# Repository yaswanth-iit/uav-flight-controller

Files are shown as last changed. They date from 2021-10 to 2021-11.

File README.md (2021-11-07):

## UAV Flight Controller
This repository consists of schematics, PCB layout, output files of UAV flight controller (Designed using kiCAD) [4-Layer]

[Schematics](https://raw.githubusercontent.com/yaswanth-iit/uav-flight-controller/master/quick%20view/schematics.pdf)

[PCB Layout](https://raw.githubusercontent.com/yaswanth-iit/uav-flight-controller/master/quick%20view/full%20pcb%20layout.pdf)

Used ICs:

* Microcontroller:  STM32F405RGT6, 25 MHz Clock
* EEPROM: 24CW1280T-I_OT
* FLASH Memory: W25N01GVZEIG_TR
* IMU: BMI088
* Magnetometer: IIS2MDCTR
* Barometer: BMP388
* PWM DRIVER: PCA9685BS
* SBUS INVERTER: 74LVC1G04GX4Z
* Voltage Regulator: LD39200PU33R
* USB TO UART: CH330
* ESD Suppressor: USBLC6-2SC6

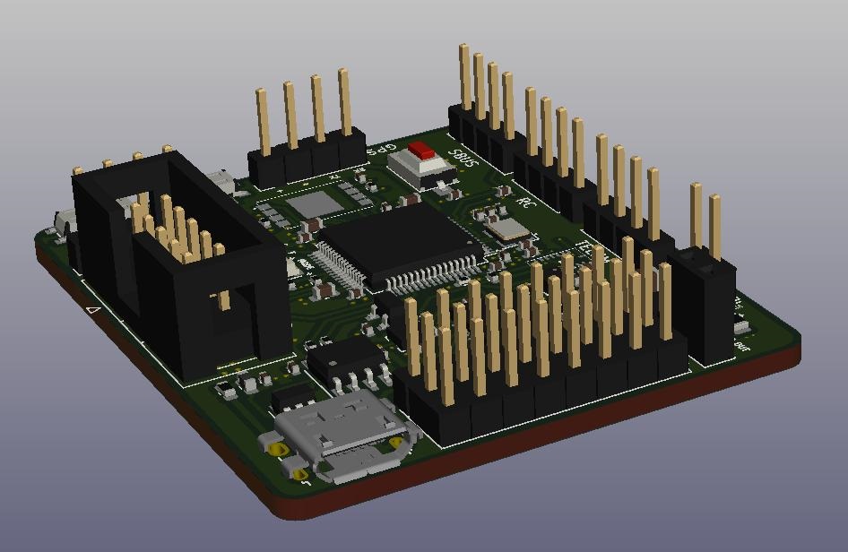
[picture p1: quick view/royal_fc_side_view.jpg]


# Top View

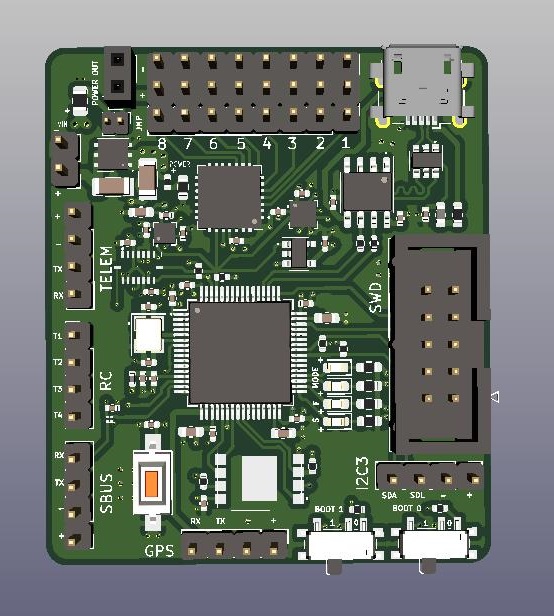
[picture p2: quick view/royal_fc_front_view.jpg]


# Bottom view

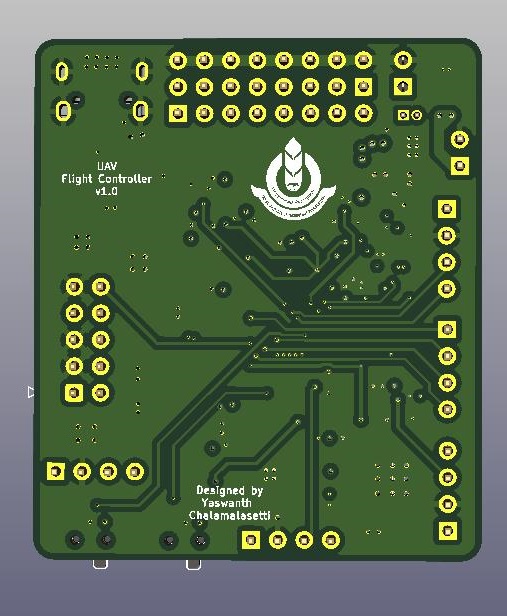
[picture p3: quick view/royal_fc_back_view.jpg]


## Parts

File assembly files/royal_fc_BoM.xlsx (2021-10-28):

Item | Qty | Reference(s) | Value | Description | Component name : PCB footprint | Manufacturer | Part Number | Availability status | Distributor
1 | 20 | C1, C3, C4, C5, C6, C8, C9, C14, C15, C16, C17, C18, C21, C22, C23, C24, C25, C26, C28, C29, | 100nF | 4.7uF+/-10% 10V X5R 1608 0603 | Capacitor_SMD:C_0402_1005Metric
2 | 1 | C2, | 4.7uF | 1UF 16V 10% 0402 | Capacitor_SMD:C_0603_1608Metric
3 | 1 | C7, | 1uF | 16V 0.1uF X5R 0402 10% | Capacitor_SMD:C_0402_1005Metric
4 | 2 | C10, C11, | 10uF | 2.2uF+/-10% 16V X5R 1608 0603 | Capacitor_SMD:C_1206_3216Metric
5 | 2 | C12, C13, | 2.2uF | 50V 18pF C0G 0402 5% | Capacitor_SMD:C_0603_1608Metric
6 | 2 | C19, C20, | 18pF | 1206 MLCC X5R 10 uF +/- 5% 10 V | Capacitor_SMD:C_0402_1005Metric
7 | 1 | C27, | 10uF | 0603 10uF+/-10% 10V X5R 1608 | Capacitor_SMD:C_0603_1608Metric
8 | 1 | C30, | 220nF | 10V 0.22uF X5R 0402 10% | Capacitor_SMD:C_0402_1005Metric
9 | 1 | D1, | Yellow | Light emitting diode | Fuse:Fuse_0402_1005Metric
10 | 1 | D2, | Green | Light emitting diode | LED_SMD:LED_0603_1608Metric
11 | 1 | D3, | Red | Light emitting diode | LED_SMD:LED_0603_1608Metric
12 | 2 | D4, D5, | Blue | Light emitting diode | LED_SMD:LED_0603_1608Metric
13 | 1 | D6, | Schottky diode | Schottky diode | D_Schottky:Diode_0805_2012Metric
14 | 1 | F1, | 500mA | Fuse 500mA | Fuse:Fuse_0603_1608Metric
15 | 1 | FB1, | 600 ohm @ 100Mhz | Ferrite bead | Ferrite_Bead_SMD:L_0402_1005Metric
16 | 1 | FB2, | 600 ohm @ 100Mhz | Ferrite bead | Ferrite_Bead_SMD:L_0603_1608Metric
17 | 1 | GPS1, | 01x04 | Generic connector, single row, 01x04 | PinHeader_1x04_P2.54mm_Vertical
18 | 1 | I2C1, | 01x04 | Generic connector, single row, 01x04 | PinHeader_1x04_P2.54mm_Vertical
19 | 1 | IC1, | LD39200PU33R | Voltage Regulator | DFN-6-1EP_3x3mm_P1mm_EP1.5x2.4mm
20 | 1 | IC2, | 24CW1280T-I_OT | EEPROM | SOT-23-5
21 | 1 | IC3, | W25N01GVZEIG_TR | FLASH memory | WSON 8x6-mm
22 | 1 | IC4, | 74LVC1G04GX4Z | SBUS Inverter | SOT1269-2
23 | 1 | IC5, | IIS2MDCTR | Magnetometer | LGA-12_2x2mm_P0.5mm
24 | 1 | J1, | 01x02 | Generic connector, single row, 01x02 | PinSocket_1x02_P2.54mm_Vertical
25 | 1 | J2, | 01x08 | Generic connector, single row, 01x08 | PinHeader_1x08_P2.54mm_Vertical
26 | 1 | J3, | 02x08 | Generic connector, double row, 02x08 | PinHeader_2x08_P2.54mm_Vertical
27 | 1 | JP1, | 01x02 | Jumper, normally open, small symbol | PinHeader_1x02_P1.27mm_Vertical
28 | 4 | R2, R9, R11, R12, | 10k | Resistor | Resistor_SMD:R_0402_1005Metric
29 | 2 | R3, R4, | 22 | Resistor | Resistor_SMD:R_0402_1005Metric
30 | 2 | R1, R5, | 2.2k | Resistor | Resistor_SMD:R_0603_1608Metric
31 | 3 | R6, R7, R8, | 1k | Resistor | Resistor_SMD:R_0603_1608Metric
32 | 4 | R13, R14, R15, R16, | 2.2k | Resistor | Resistor_SMD:R_0402_1005Metric
33 | 1 | RC1, | 01x04 | Generic connector, single row, 01x04 | PinHeader_1x04_P2.54mm_Vertical
34 | 2 | S1, S2, | TDD01H0SB1R | SPDT switches | Button_Switch_SMD:SW_SPDT_PCM12
35 | 1 | S3, | SPDT | Push button switch, generic, two pins | Button_Switch_SMD:SW_SPST_CK_RS282G05A3
36 | 1 | SBUS1, | 01x04 | Generic connector, single row, 01x04 | PinHeader_1x04_P2.54mm_Vertical
37 | 1 | SWD1, | 02x05 | Generic connector, double row, 02x05 | IDC-Header_2x05_P2.54mm_Vertical
38 | 1 | TELEM1, | 01x04 | Generic connector, single row, 01x04 | PinHeader_1x04_P2.54mm_Vertical
39 | 1 | U1, | USBLC6-2SC6 | Very low capacitance ESD protection diode, 2 data-line, SOT-23-6 | SOT-23-6
40 | 1 | U2, | CH330N | USB serial converter, UART, SOIC-8 | SOIC-8_3.9x4.9mm_P1.27mm
41 | 1 | U3, | STM32F405RGTx | ARM Cortex-M4 MCU, 1024KB flash, 128KB RAM, 168MHz, 1.8-3.6V, 51 GPIO, LQFP-64 | LQFP-64_10x10mm_P0.5mm
42 | 1 | U4, | BMP388 | Barometer | Package_LGA:ST_HLGA-10_2.5x2.5mm_P0.6mm_LayoutBorder3x2y
43 | 1 | U5, | PCA9685BS | 16-channel 12-bit PWM Fm+ I2C-bus LED controller RGBA QFN | QFN-28-1EP_6x6mm_P0.65mm_EP4.25x4.25mm
44 | 1 | U6, | BMI088 | Accelerometer + Gyrometer | LGA 3.0mm x 4.5mm x 0.95mm
45 | 1 | USB1, | USB_B_Micro | USB Micro Type B connector | Connector_USB:USB_Micro-B_Wuerth_629105150521_CircularHoles
46 | 1 | VIN1, | 01x02 | Generic connector, single row, 01x02 | Connector_PinHeader_2.54mm:PinHeader_1x02_P2.54mm_Vertical
47 | 1 | Y1, | 25MHz | Four pin crystal, GND on pins 2 and 4, small symbol | Crystal:Crystal_SMD_3225-4Pin_3.2x2.5mm

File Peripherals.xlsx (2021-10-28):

S.No | Component | Model Number | Supports | Choosen | I2C1 Address | Max Voltage | Max Current
1 | uC: | STM32F405RGT6 |  |  |  | 3.3V | 240 mA | I/O = 25mA
2 | Regulator: | LD39200 PU33R |  |  |  | 3.3V | 2A | 1A is sufficient
3 | USB_B_MICRO: | USBLC6-2SC6 |  |  |  | 5V | 150nA
4 | USB 2 SERIAL | CH330 |  |  |  | 5V | 300uA
5 | FLASH: | W25N01GVZEIG_TR |  | SPI |  | 3.3V | 25mA
6 | EEPROM: | 24CW1280T-I_OT |  | I2C1 | 0x50 | 3.3V | 1mA
7 | IMU: | BMI088 | I2C & SPI | I2C1 | 0x19 (ACC) 0x69 (GYR) | 3.3V | 5mA
8 | Magnetometer: | MAG1-IIS2MDCTR | I2C & SPI | I2C1 | 0x1E | 3.3V | 1mA
9 | Barometer: | BMP388 | I2C & SPI | I2C1 | 0x76 | 3.3V | 1.2mA
10 | PWM DRIVER: | PCA9685BS |  | I2C1 | 0x40 | 3.3V | 30mA | LED source = 10mA | LED sink = 25mA
11 | SBUS INVERTER: | 74LVC1G04GX4Z |  |  |  | 3.3V | 100mA

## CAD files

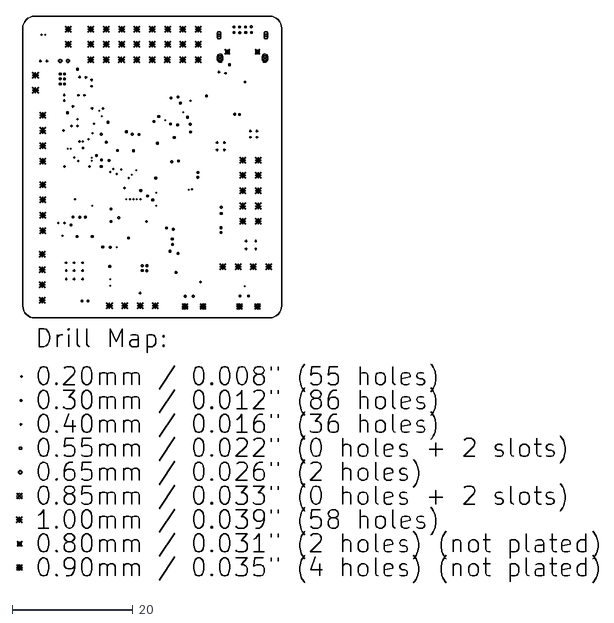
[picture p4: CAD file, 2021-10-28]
kicad sch & pcb files/royal_fc-drl_map.dxf
96.4 x 93.9

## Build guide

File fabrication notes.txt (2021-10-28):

1.  FABRICATE PER ANSI/IPC-A-600,IPC-QE-605, IPC-4101,IPC-4552 AND IPC-SM-840 SPECIFICATIONS. 
2.  MATERIAL: BASE MATERIAL LAMINATED EPOXY GLASS NEMA GRADE FR-4, NOM .062", COLOR NATURAL.  
    NOM 1 OZ COPPER WEIGHT.   THICKNESS .070" MAX AFTER PLATING AND FINISHING.  
    PREFER ROHS COMPLIANT PER IPC-4101 SLASH SHEETS #26 OR #83 OR #98 WITH 
    MINIMUM TG 135 DEGREE C OR HIGHER, TD 300 DEGREE C OR HIGHER AND FLAME RATED UL 94V-0.
3.  ALL DIMENTIONS ARE IN INCHES UNLESS OTHERWISE SPECIFIED
4.  DIMENSIONAL TOLERANCES ARE: .XX=+/- .01; .XXX=+/-.005;
5.  TOTAL THICHNESS OF PCB AFTER PLATING SHALL BE 0.0618" +/- 0.005"
6.  SOLDERMASK BOTH SIDES OF BOARD OVER BARE COPPER WITH MATERIAL PER ANSI/IPC-SM-840, 
    COLOR SHALL BE GREEN AND SOLVENT FREE
7.  APPLY SOLDER PLATING WITH HOT-AIR LEVELING TO EXPOSED COPPER BOTH SIDES.  
    LEAD-FREE SOLDER PREFERRED; LEADED SOLDER ACCEPTABLE.
8.  APPLY SILKSCREEN TO TOP SIDE OF BOARD USING NON-CONDUCTIVE WHITE EPOXY INK. NO INK SHALL BE ON EXPOSED PADS
9.  SEE SEPARATE DRILL FILE FOR HOLE LOCATIONS.  
10.  HOLE LOCATIONS SPECIFIED IN SEPARATE DRILL FILE TAKE PRECEDENCE OVER THIS DWG AND ARTWORK. 
     CONTACT IIT BHUBANESWAR TO RESOLVE DIMENSION CONFLICTS BETWEEN DWG AND ARTWORK.
     NO ALTERATIONS TO GERBER FLES WITHOUT PRIOR CONSENT FROM IIT BHUBANESWAR
11.  HOLE SIZES ARE SPECIFIED AS FINAL DIMENSIONS AFTER PLATING AND FINISHING.  
     UNLESS OTHERWISE SPECIFIED ALL HOLES TO BE PLATED. 
12.  VENDOR TO PLATE HOLES AND EXPOSED PADS.
     VENDOR TO SPECIFY TYPE OF PLATING MATERIAL TO BE USED WHEN ACCEPTING ORDER.
13.  IT IS VENDOR'S RESPONSIBILITY TO SELECT THE BASE MATERIAL TO YIELD THE SPECIFIED IMPEDENCE CHARACTERISTICS TO WITHIN +/-10%
14.  ALL HOLES SHALL BE LOCATED WITHIN 0.003" DIAMETER OF TRUE POSITION OR OTHER TRUE POSITION
15.  WARP OR TWIST OF BOARD SHALL NOT EXCEED 0.01 INCH PER INCH
16.  REMOVE ALL BURRS AND BREAK SHARP EDGES 0.015" MAX
17.  PLATED THRU HOLES & EXPOSED PADS SHALL BE TIN/LEAD PLATED 0.0003" TO 0.0005" THICK
18.  ONLY VENDOR IDENTIFICATION MARK & ORDER NUMBER CAN BE ADDED ONLY AT THE SPECIFIED LOCATION (UNDER THE IC). AFTER ASSEMBLY IT SHOULD NOT APPEAR OUTSIDE
19.  MANUFACTURER SHOULD NOT ADD ANY OTHER DATA EXCEPT ABOVE MENTIONED LIKE NAME, LOGO, DATE CODE, UL LISTING OR ANY OTHER MARKING TO ANY VISIBLE LAYER
20.  AFTER ASSEMBLY TRIM SOLDER FILLETS AND COMPONENT LEADS TO 0.06" (MAX) 
     BEYOND BOARD SURFACE ON BOTTOM SIDE.
21. BOARDS MUST PASS VISUAL INSPECTION PER IPC-A-600 CLASS 2
22. FINISHED BOARD MUST MEET UL94V-0 RATING AND ROHS COMPLIANCE
23. DOCUMENTATION THAT MUST BE DELIVERED WITH BOARDS:
	- CROSS SECTION REPORT (SPACING BETWEEN COPPER LAYERS AND COPPER THICHNESS)
	- ELECTRICAL TEST CERTIFICATION OF COMPILANCE (ACC. TO IPC-ET-652 CLASS 2)
	- CERTIFICATION OF COMPILANCE (BOARD HAS BEEN MANUFACTURED TO DRAWING REQUIREMENTS)
	- ROHS CERTIFICATION OF COMPILANCE

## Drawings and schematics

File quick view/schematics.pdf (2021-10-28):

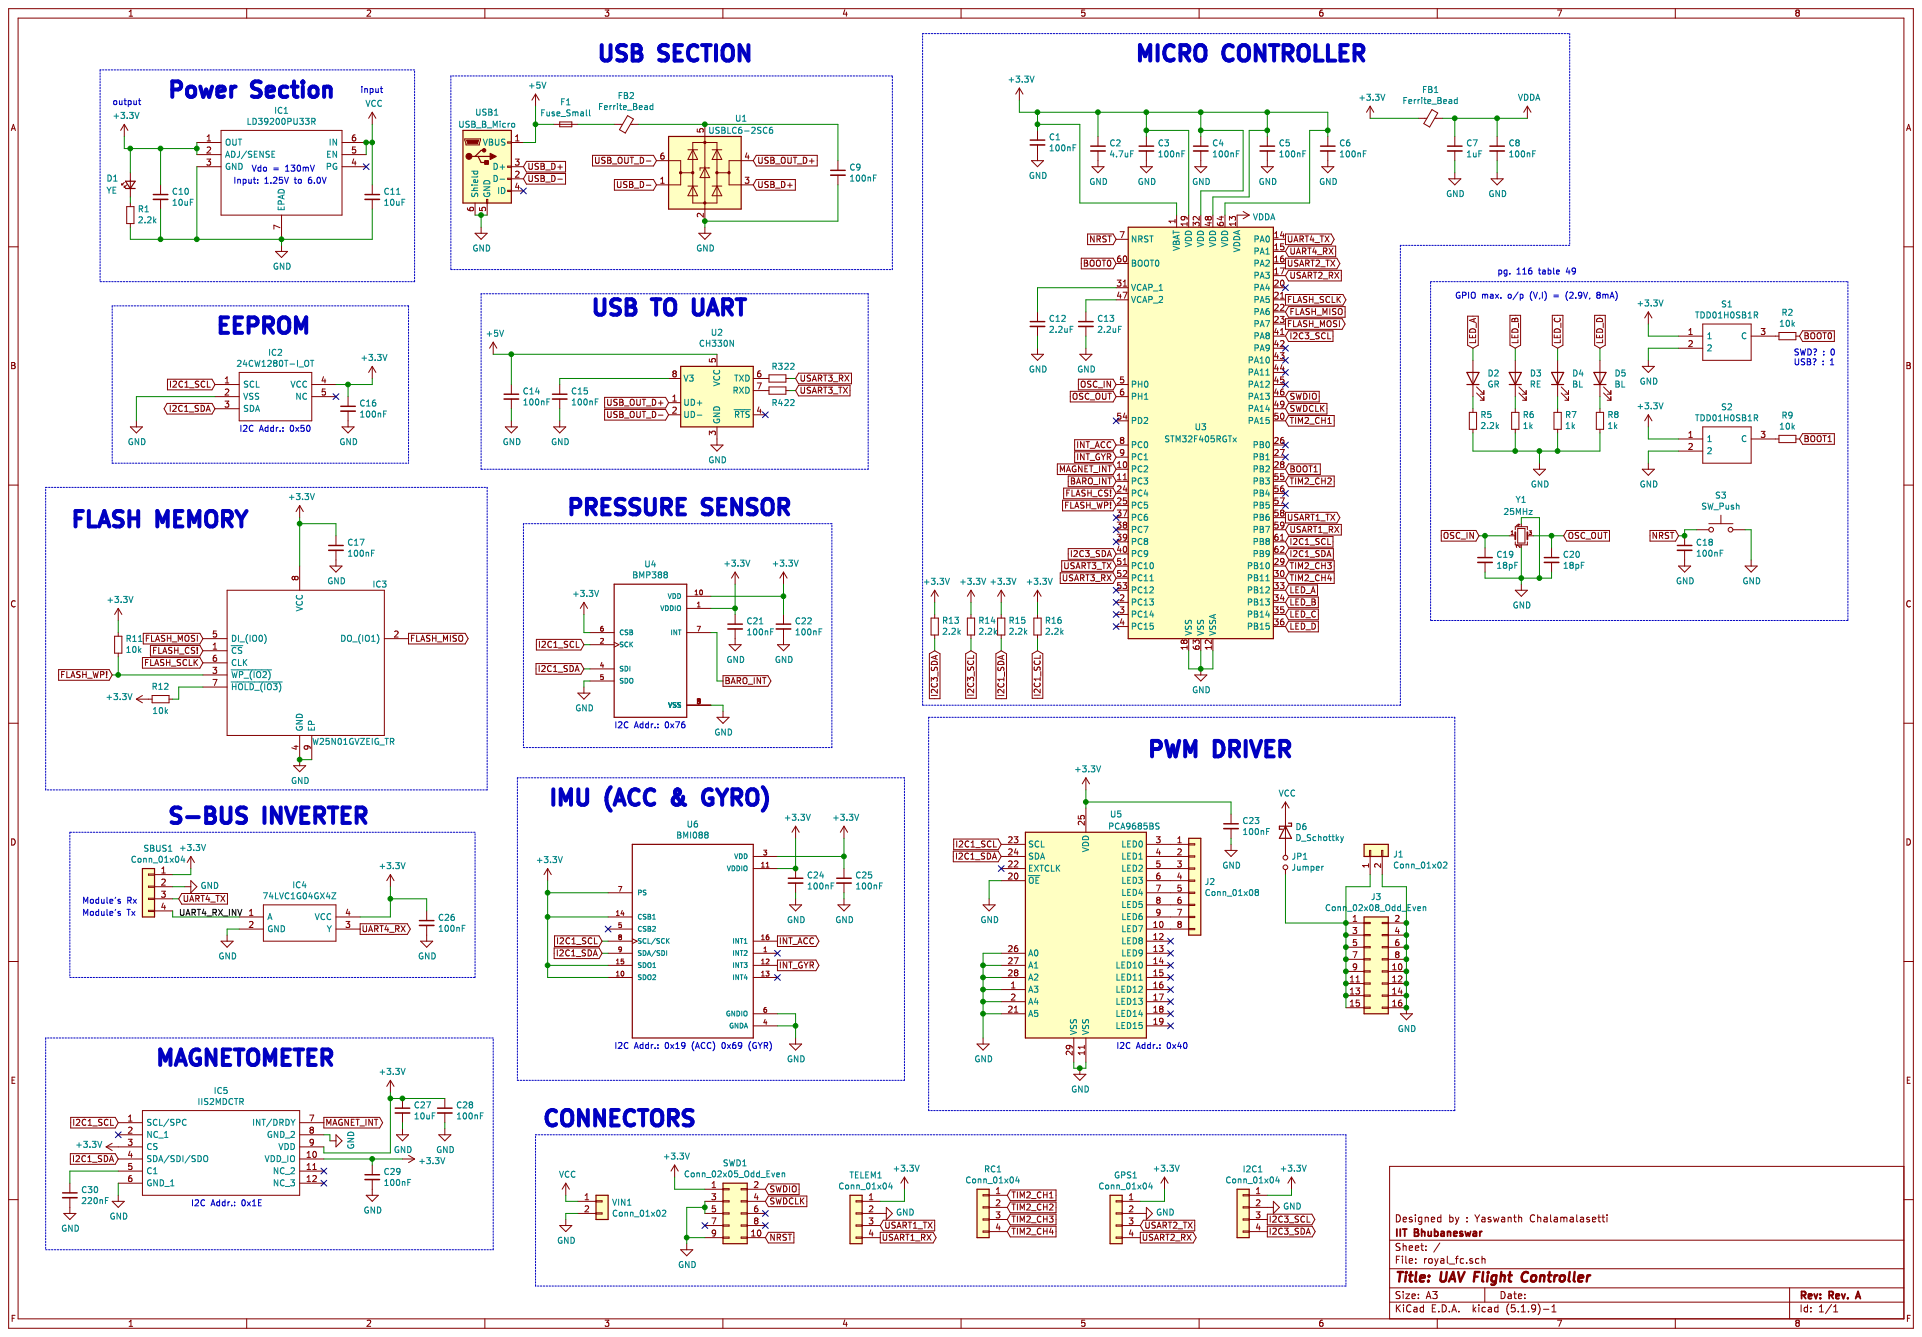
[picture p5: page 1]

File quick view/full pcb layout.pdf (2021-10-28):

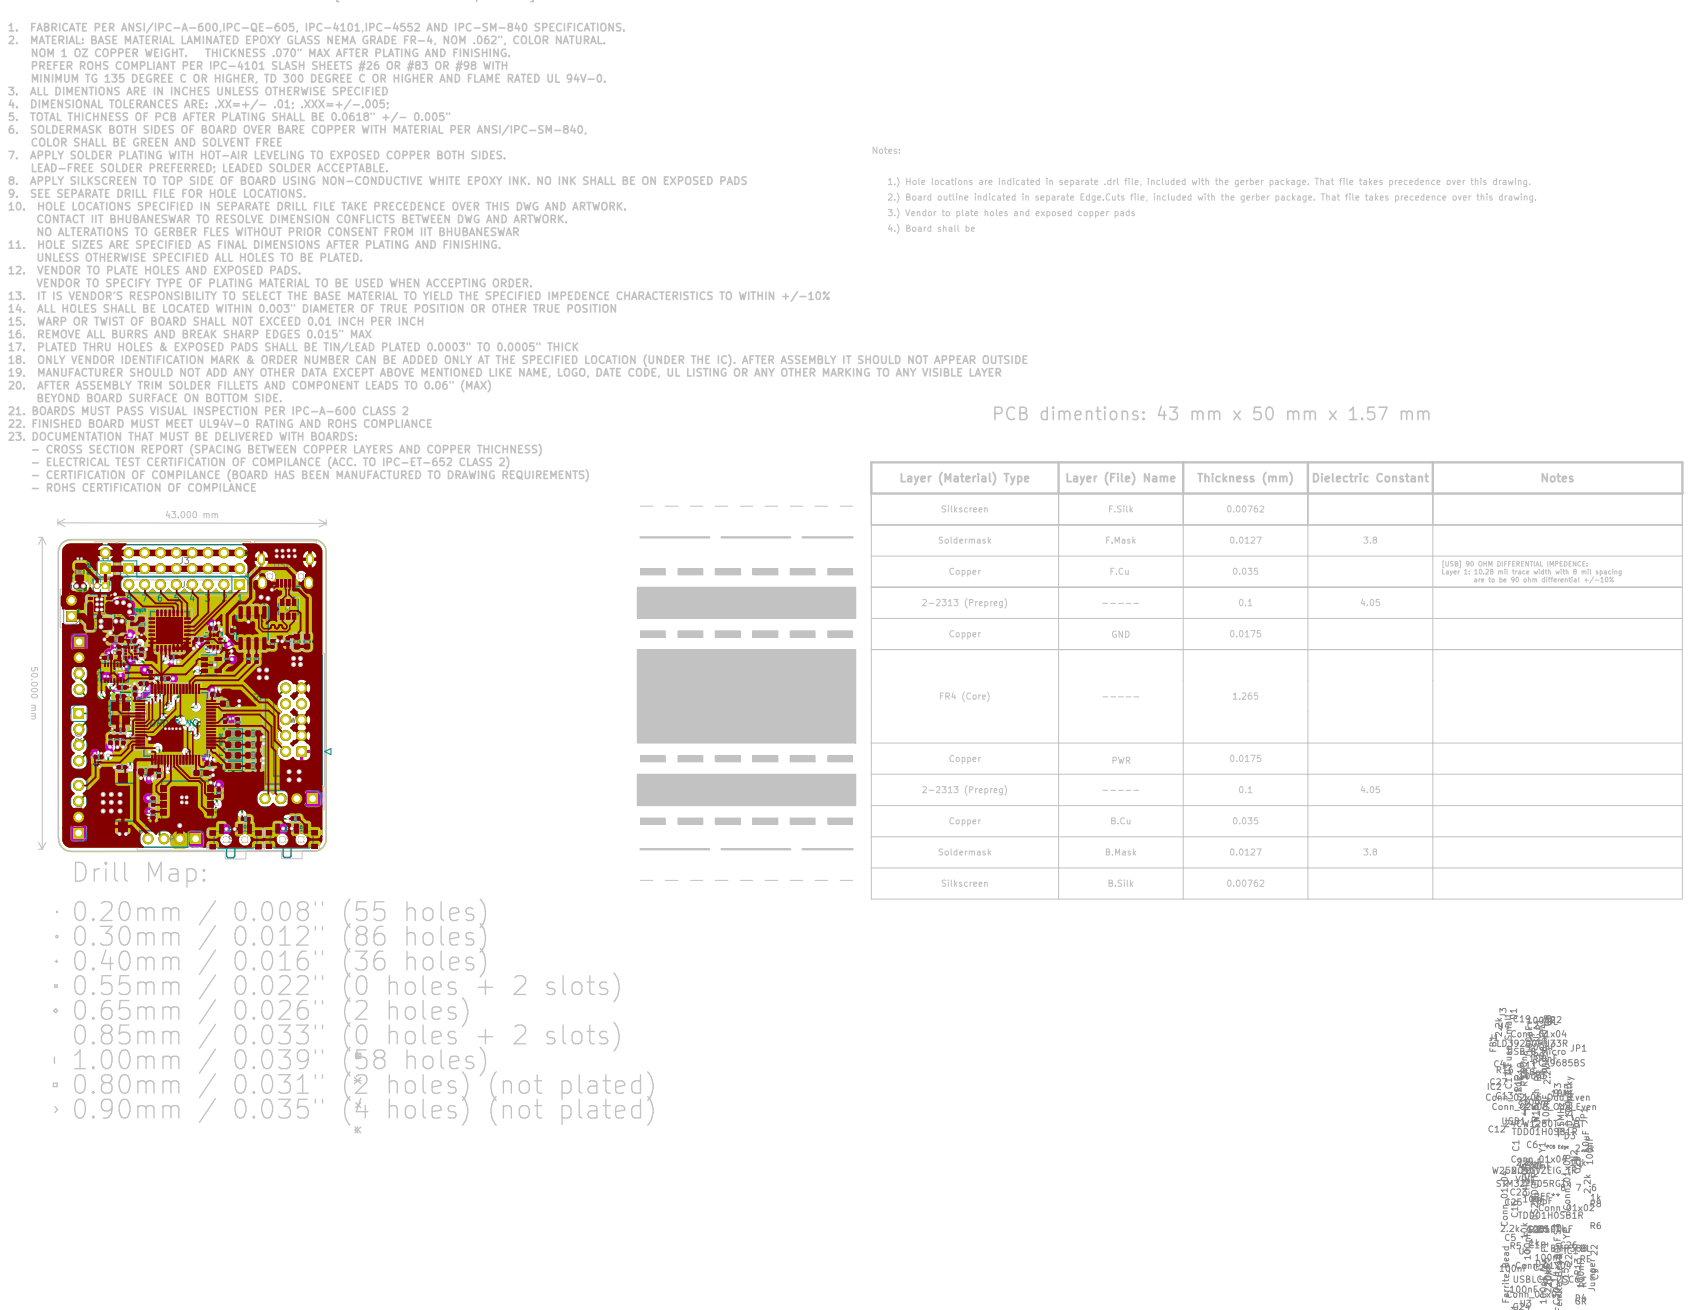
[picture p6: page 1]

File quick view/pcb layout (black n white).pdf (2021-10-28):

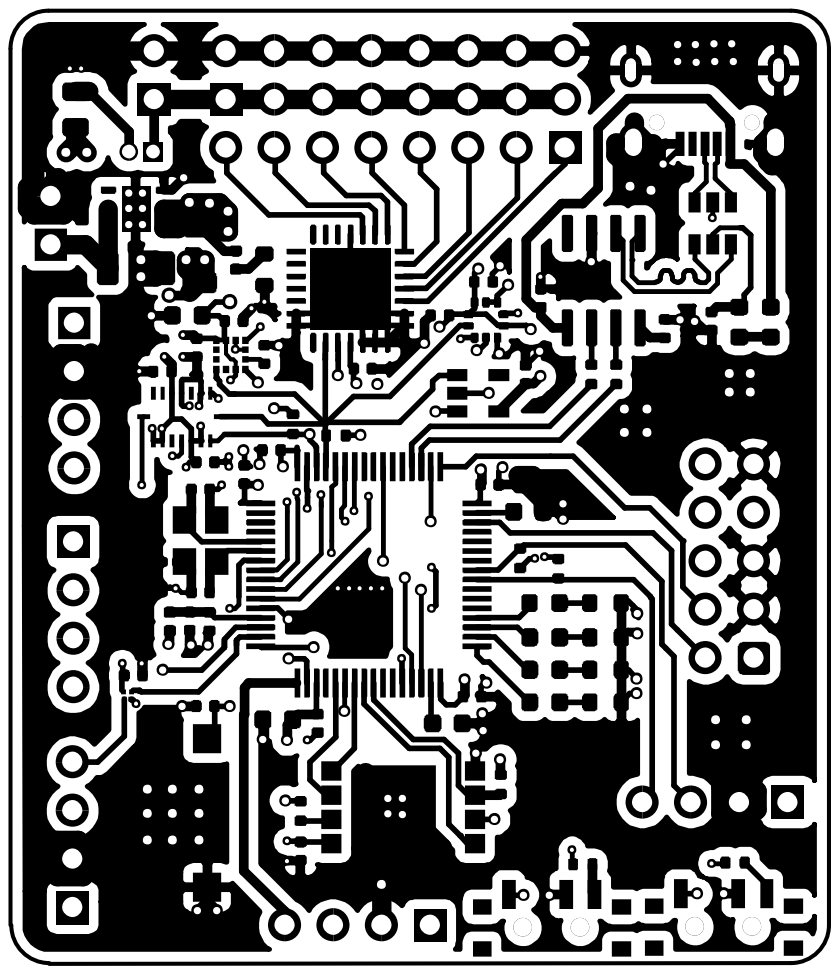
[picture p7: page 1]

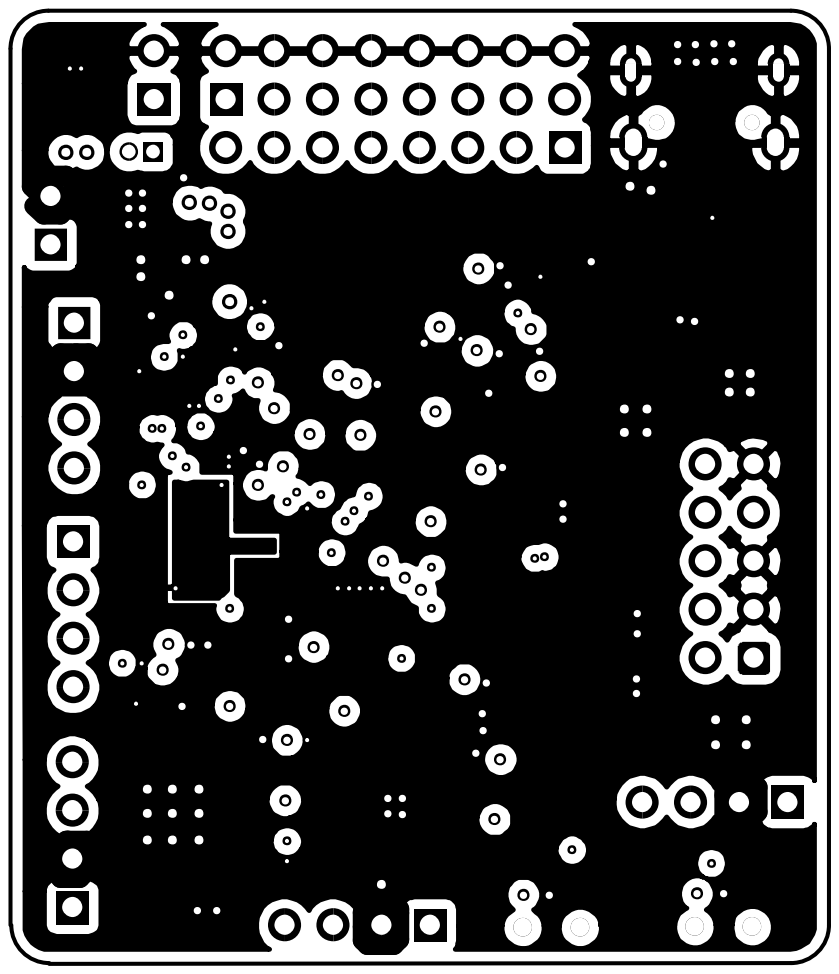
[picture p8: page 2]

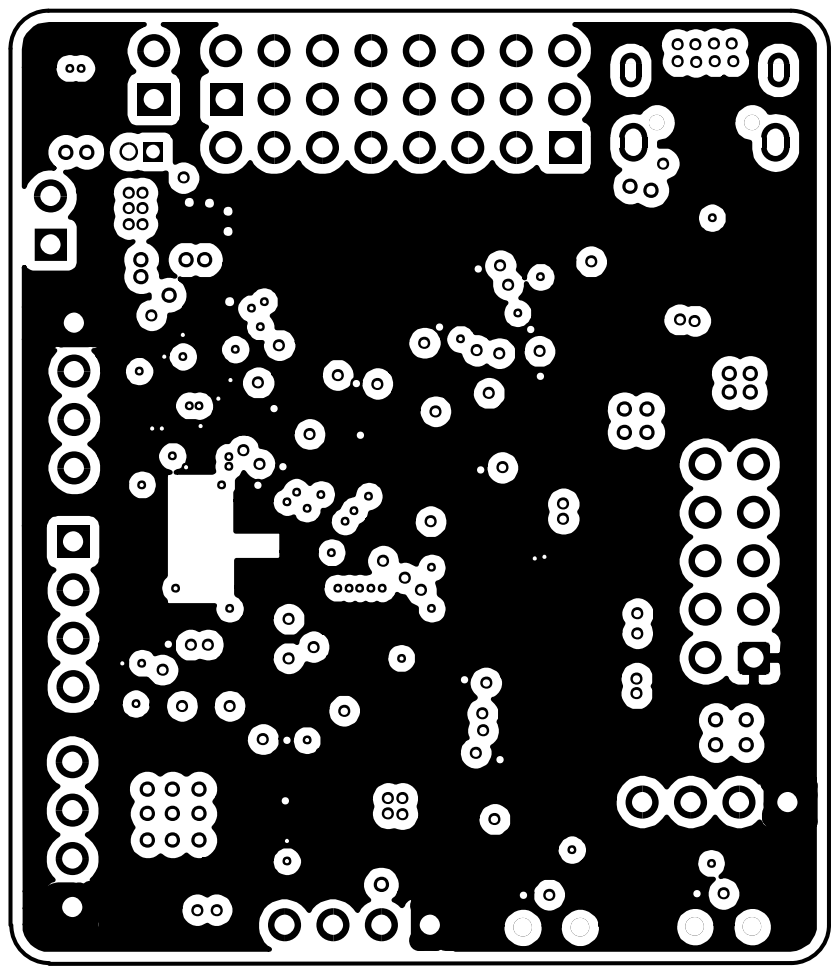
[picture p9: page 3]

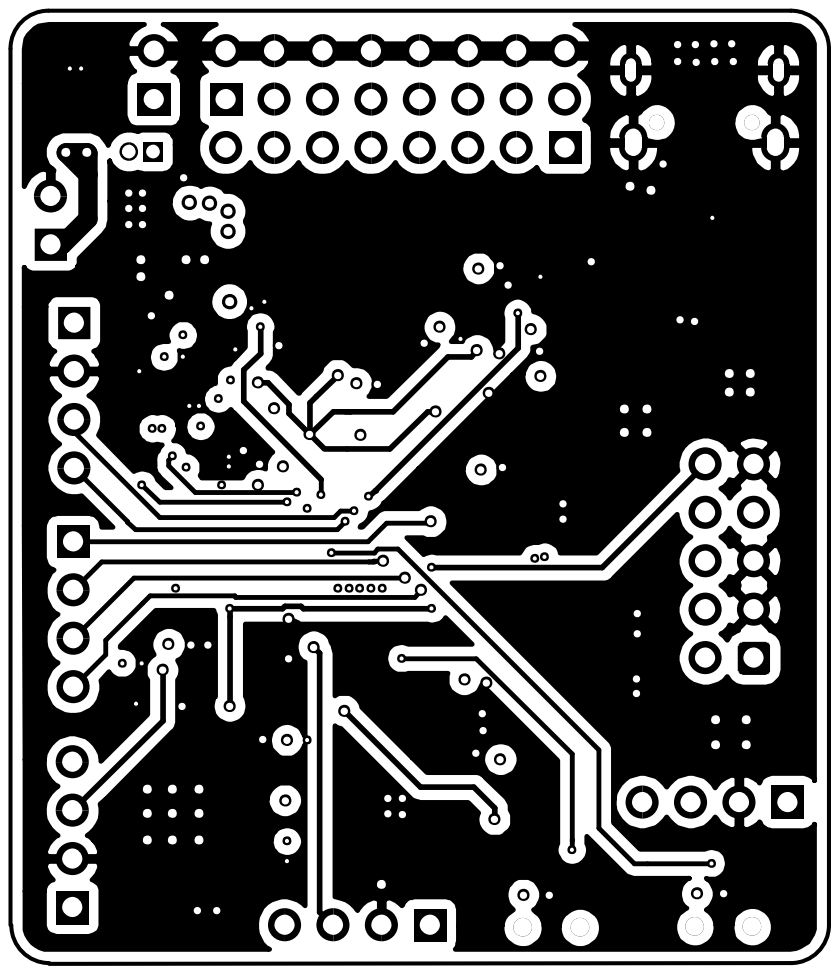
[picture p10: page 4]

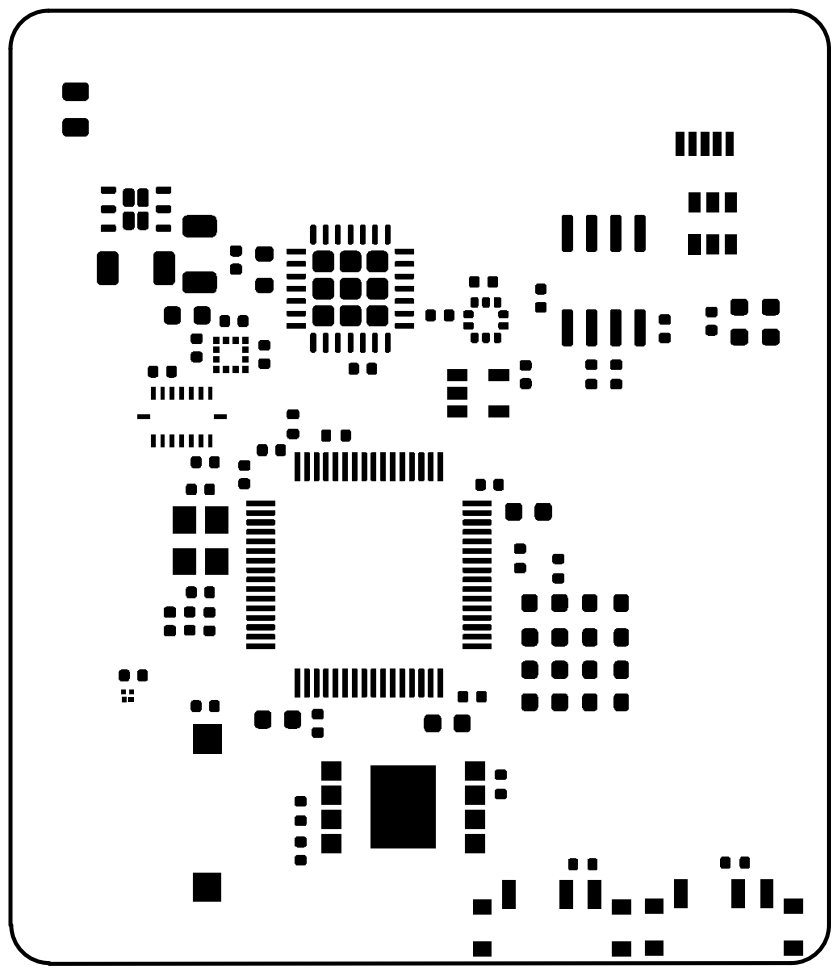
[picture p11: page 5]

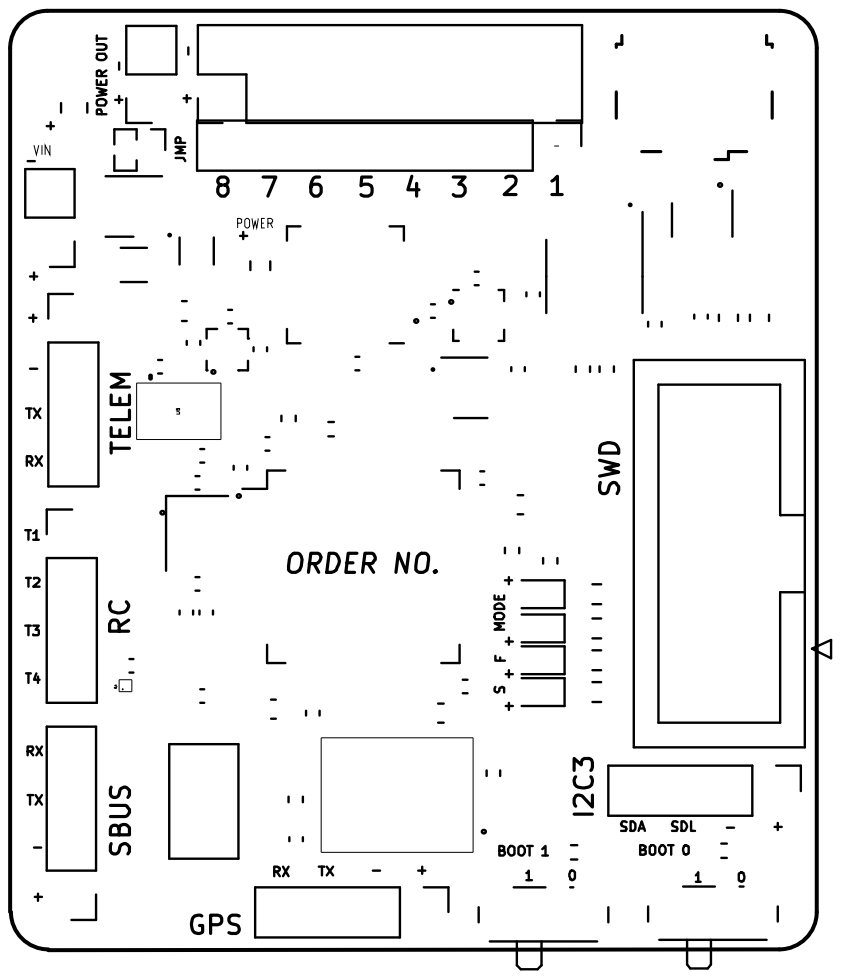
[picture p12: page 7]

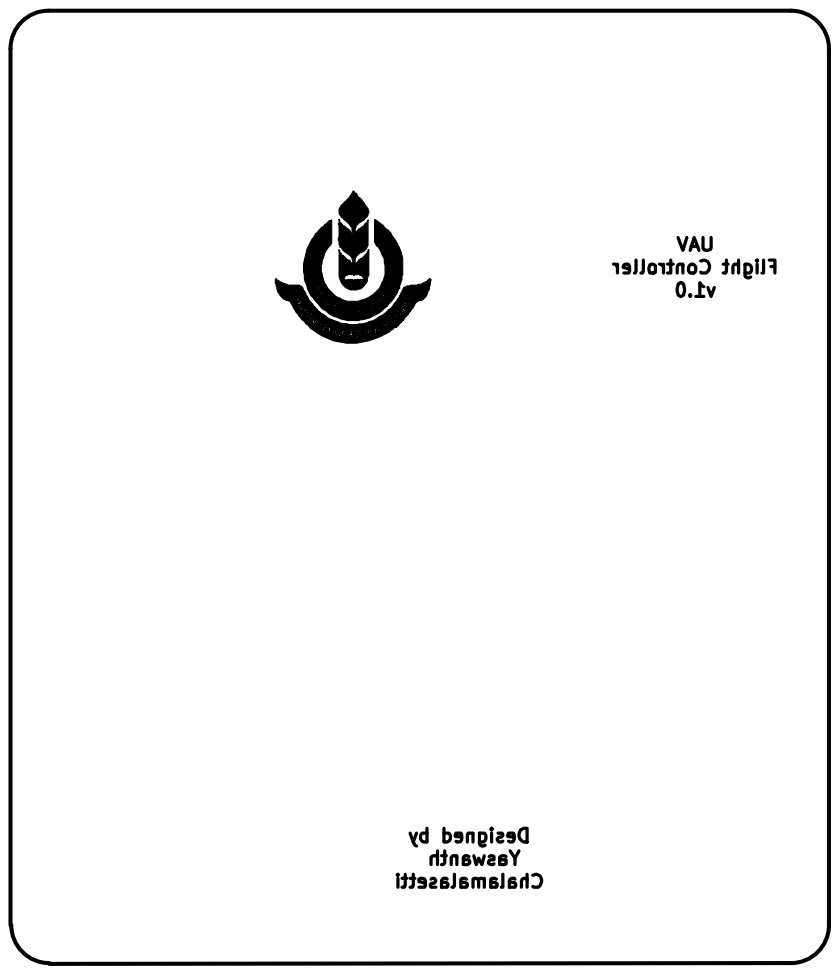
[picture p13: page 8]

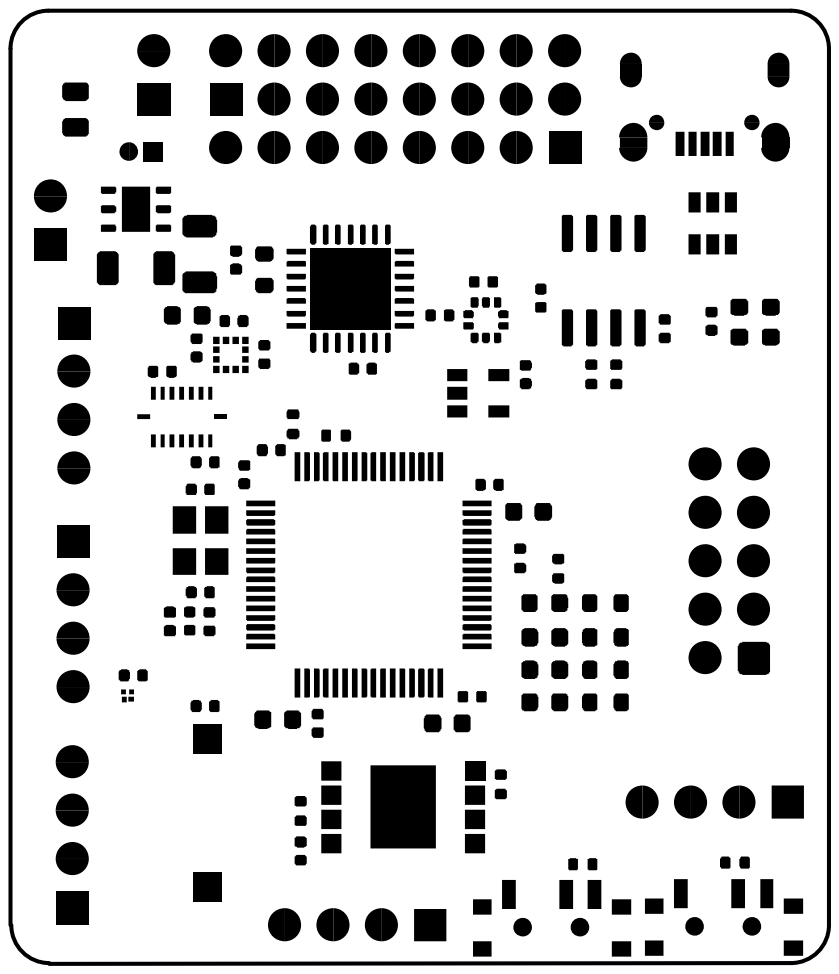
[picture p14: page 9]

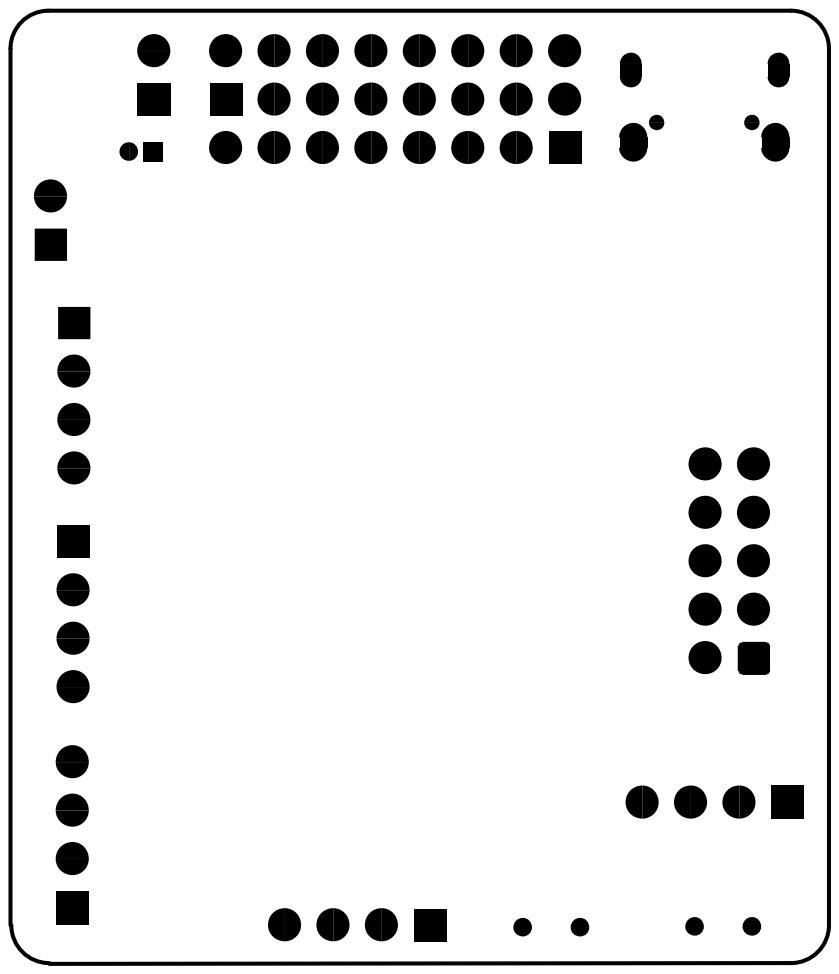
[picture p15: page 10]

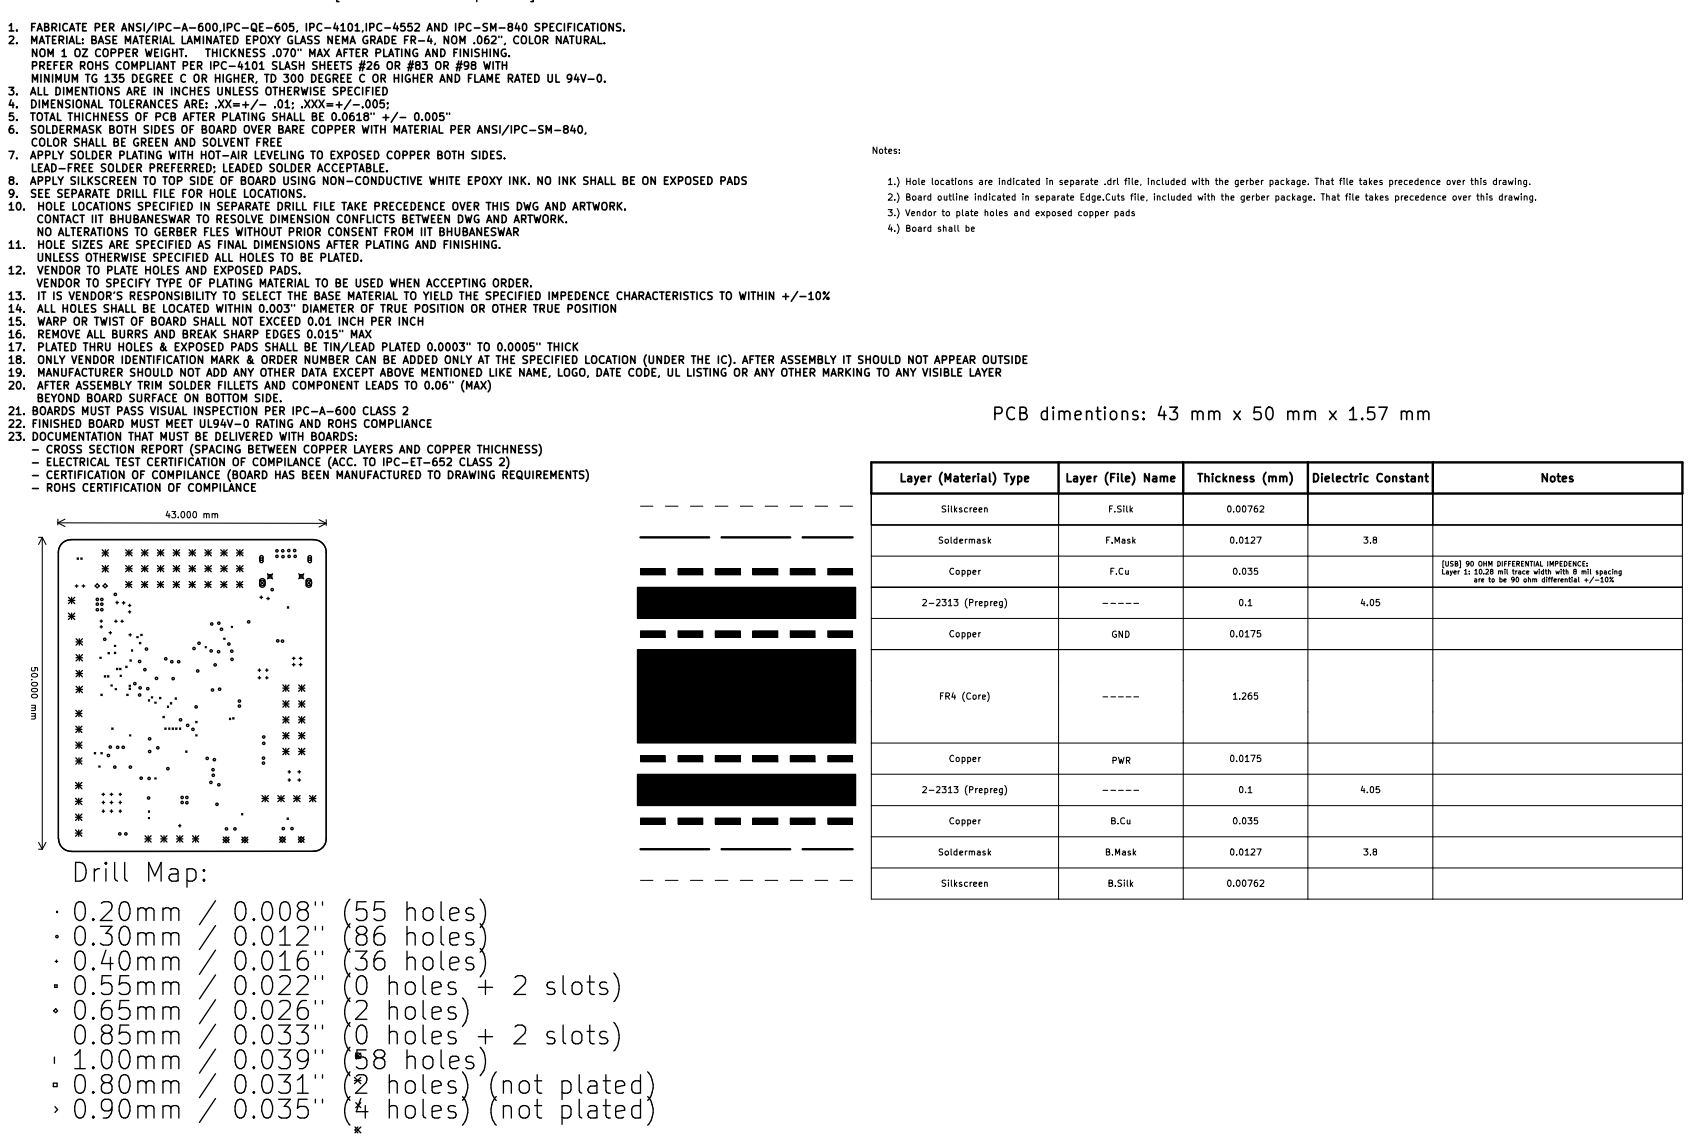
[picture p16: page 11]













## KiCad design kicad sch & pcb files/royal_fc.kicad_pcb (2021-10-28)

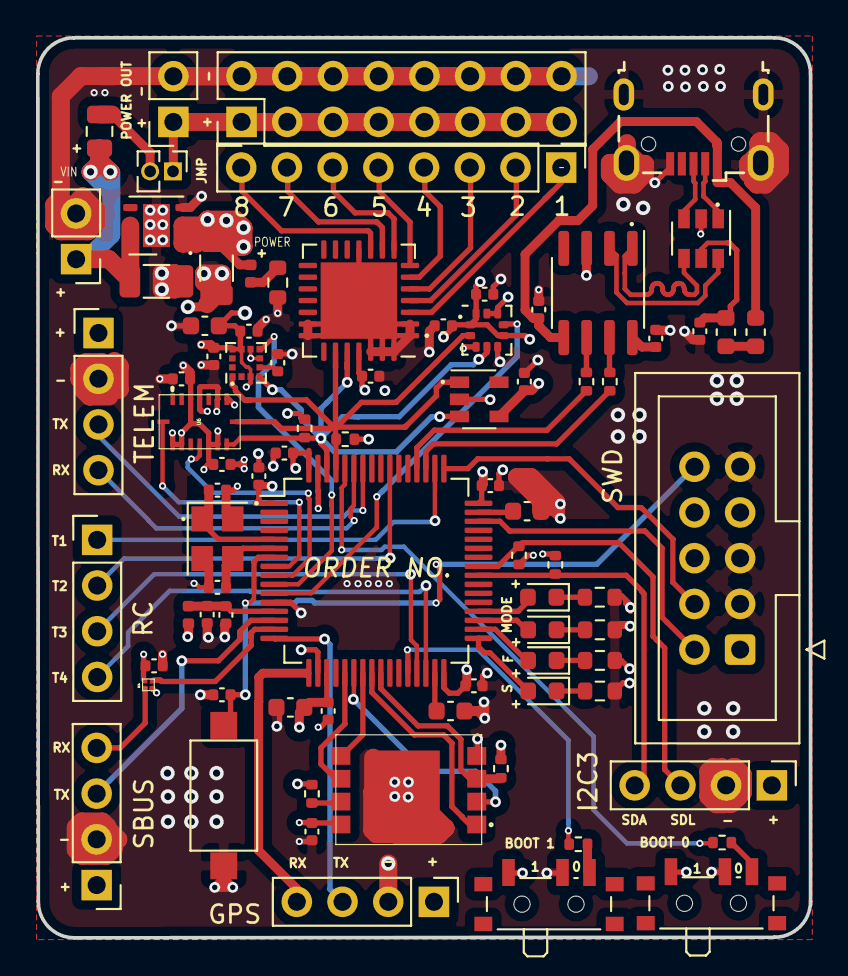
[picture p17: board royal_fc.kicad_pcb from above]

Board: 4 copper layers, 42.9 x 50.0 mm, 81 parts (0 on the bottom side), 72 nets.

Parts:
8  7  6: Conn_01x08; PinHeader_1x08_P2.54mm_Vertical
C1, C3, C4, C5, C6, C8, C9, C14, C15, C16, C17, C18, C21, C22, C23, C24, C25, C26, C28, C29: 100nF; C_0402_1005Metric
C2: 4.7uF; C_0603_1608Metric
C7: 1uF; C_0402_1005Metric
C10, C11: 10uF; C_1206_3216Metric
C12, C13: 2.2uF; C_0603_1608Metric
C19, C20: 18pF; C_0402_1005Metric
C27: 10uF; C_0603_1608Metric
C30: 220nF; C_0402_1005Metric
D1: YE; Fuse_0402_1005Metric
D2: GR; LED_0603_1608Metric
D3: RE; LED_0603_1608Metric
D4, D5: BL; LED_0603_1608Metric
D6: D_Schottky; Fuse_0805_2012Metric
F1: Fuse_Small; Fuse_0603_1608Metric
FB1: Ferrite_Bead; L_0402_1005Metric
GPS: Conn_01x04; PinHeader_1x04_P2.54mm_Vertical
I2C3: Conn_01x04; PinHeader_1x04_P2.54mm_Vertical
IC1: LD39200PU33R; DFN-6-1EP_3x3mm_P1mm_EP1.5x2.4mm
IC2: 24CW1280T-I_OT; SOT-23-5
IC3: W25N01GVZEIG_TR
IC4: 74LVC1G04GX4Z; 74LVC1G04
IC5: IIS2MDCTR; LGA-12_2x2mm_P0.5mm
J1: Conn_01x02; PinSocket_1x02_P2.54mm_Vertical
J2: Ferrite_Bead; L_0603_1608Metric
J3: Conn_02x08_Odd_Even; PinHeader_2x08_P2.54mm_Vertical
JP1: Jumper; PinHeader_1x02_P1.27mm_Vertical
JP1#2: 1k; R_0603_1608Metric
R1: R1; R_0603_1608Metric
R2, R9, R11, R12: 10k; R_0402_1005Metric
R3, R4: 22; R_0402_1005Metric
R5: 2.2k; R_0603_1608Metric
R6, R8: 1k; R_0603_1608Metric
R13, R14, R15, R16: 2.2k; R_0402_1005Metric
RC: Conn_01x04; PinHeader_1x04_P2.54mm_Vertical
S1, S2: TDD01H0SB1R; SW_SPDT_PCM12
S3: SW_Push; SW_SPST_CK_RS282G05A3
SBUS: Conn_01x04; PinHeader_1x04_P2.54mm_Vertical
SWD1: Conn_02x05_Odd_Even; IDC-Header_2x05_P2.54mm_Vertical
TELEM: Conn_01x04; PinHeader_1x04_P2.54mm_Vertical
U1: USBLC6-2SC6; SOT-23-6
U2: CH330N; SOIC-8_3.9x4.9mm_P1.27mm
U3: STM32F405RGTx; LQFP-64_10x10mm_P0.5mm
U4: BMP388; ST_HLGA-10_2.5x2.5mm_P0.6mm_LayoutBorder3x2y
U5: PCA9685BS; QFN-28-1EP_6x6mm_P0.65mm_EP4.25x4.25mm
U6: BMI088; BMI008
USB1: USB_B_Micro; USB_Micro-B_Wuerth_629105150521
VIN1: Conn_01x02; PinHeader_1x02_P2.54mm_Vertical
Y1: 25MHz; Crystal_SMD_3225-4Pin_3.2x2.5mm

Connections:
+3V3: C1.1, C2.1, C3.1, C4.1, C5.1, C6.1, C10.1, C16.1, C17.1, C21.1, C22.1, C23.1, C24.1, C25.1, C26.1, C27.1, C28.1, C29.1, D1.2, FB1.2, GPS.1, I2C3.1, IC1.1, IC1.2, IC2.4, IC3.8, IC4.4, IC5.3, IC5.9, IC5.10, R11.2, R12.1, R13.2, R14.2, R15.2, R16.2, S1.1, S2.1, SBUS.1, SWD1.1, TELEM.1, U3.1, U3.19, U3.32, U3.48, U3.64, U4.1, U4.6, U4.10, U5.25, U6.3, U6.7, U6.10, U6.11, U6.14, U6.15
+5V: C14.1, F1.1, U2.5, USB1.1
/UART4_RX_INV: IC4.1, SBUS.4
BARO_INT: U3.11, U4.7
BOOT0: R2.1, U3.60
BOOT1: R9.1, U3.28
FLASH_CS!: IC3.1, U3.24
FLASH_MISO: IC3.2, U3.22
FLASH_MOSI: IC3.5, U3.23
FLASH_SCLK: IC3.6, U3.21
FLASH_WP!: IC3.3, R11.1, U3.25
GND: C1.2, C2.2, C3.2, C4.2, C5.2, C6.2, C7.2, C8.2, C9.2, C10.2, C11.2, C12.2, C13.2, C14.2, C15.2, C16.2, C17.2, C18.2, C19.2, C20.2, C21.2, C22.2, C23.2, C24.2, C25.2, C26.2, C27.2, C28.2, C29.2, C30.2, GPS.2, I2C3.2, IC1.3, IC1.7, IC2.2, IC3.4, IC3.9, IC4.2, IC5.6, IC5.8, J1.2, J3.2, J3.4, J3.6, J3.8, J3.10, J3.12, J3.14, J3.16, JP1#2.1, R1.1, R5.1, R6.1, R8.1, S1.2, S2.2, S3.2, SBUS.2, SWD1.3, SWD1.5, SWD1.9, TELEM.2, U1.2, U2.3, U3.12, U3.18, U3.63, U4.3, U4.5, U4.8, U4.9, U5.1, U5.2, U5.11, U5.20, U5.21, U5.26, U5.27, U5.28, U5.29, U6.4, U6.6, USB1.5, USB1.6, VIN1.2, Y1.2, Y1.4
I2C1_SCL: IC2.1, IC5.1, R16.1, U3.61, U4.2, U5.23, U6.8
I2C1_SDA: IC2.3, IC5.4, R15.1, U3.62, U4.4, U5.24, U6.9
I2C3_SCL: I2C3.3, R14.1, U3.41
I2C3_SDA: I2C3.4, R13.1, U3.40
INT_ACC: U3.8, U6.16
INT_GYR: U3.9, U6.12
LED_A: D2.2, U3.33
LED_B: D3.2, U3.34
LED_C: D4.2, U3.35
LED_D: D5.2, U3.36
MAGNET_INT: IC5.7, U3.10
NRST: C18.1, S3.1, SWD1.10, U3.7
unnamed: C9.1, J2.1, U1.5
unnamed: C12.1, U3.31
unnamed: C13.1, U3.47
unnamed: C15.1, U2.8
unnamed: C30.1, IC5.5
unnamed: D1.1, R1.2
unnamed: D2.1, R5.2
unnamed: D3.1, R6.2
unnamed: D4.1, JP1#2.2
unnamed: D5.1, R8.2
unnamed: D6.2, JP1.2
unnamed: F1.2, J2.2
unnamed: IC3.7, R12.2
unnamed: J1.1, J3.1, J3.3, J3.5, J3.7, J3.9, J3.11, J3.13, J3.15, JP1.1
unnamed: 8 7 6.1, U5.3
unnamed: 8 7 6.2, U5.4
unnamed: 8 7 6.3, U5.5
unnamed: 8 7 6.4, U5.6
unnamed: 8 7 6.5, U5.7
unnamed: 8 7 6.6, U5.8
unnamed: 8 7 6.7, U5.9
unnamed: 8 7 6.8, U5.10
unnamed: R2.2, S1.3
unnamed: R3.2, U2.6
unnamed: R4.2, U2.7
unnamed: R9.2, S2.3
OSC_IN: C19.1, U3.5, Y1.1
OSC_OUT: C20.1, U3.6, Y1.3
SWDCLK: SWD1.4, U3.49
SWDIO: SWD1.2, U3.46
TIM2_CH1: RC.1, U3.50
TIM2_CH2: RC.2, U3.55
TIM2_CH3: RC.3, U3.29
TIM2_CH4: RC.4, U3.30
UART4_RX: IC4.3, U3.15
UART4_TX: SBUS.3, U3.14
USART1_RX: TELEM.4, U3.59
USART1_TX: TELEM.3, U3.58
USART2_RX: GPS.4, U3.17
USART2_TX: GPS.3, U3.16
USART3_RX: R3.1, U3.52
USART3_TX: R4.1, U3.51
USB_D+: U1.3, USB1.3
USB_D-: U1.1, USB1.2
USB_OUT_D+: U1.4, U2.1
USB_OUT_D-: U1.6, U2.2
VCC: C11.1, D6.1, IC1.5, IC1.6, VIN1.1
VDDA: C7.1, C8.1, FB1.1, U3.13

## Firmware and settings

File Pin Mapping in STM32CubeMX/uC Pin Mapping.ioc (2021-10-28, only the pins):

Mcu.UserName=STM32F405RGTx
PA0-WKUP.Signal=UART4_TX
PA1.Signal=UART4_RX
PA13.Signal=SYS_JTMS-SWDIO
PA14.Signal=SYS_JTCK-SWCLK
PA2.Signal=USART2_TX
PA3.Signal=USART2_RX
PA5.Signal=SPI1_SCK
PA6.Signal=SPI1_MISO
PA7.Signal=SPI1_MOSI
PA8.Signal=I2C3_SCL
PB10.Signal=S_TIM2_CH3
PB11.Signal=S_TIM2_CH4
PB12.GPIO_Label=LED A
PB12.Signal=GPIO_Output
PB13.GPIO_Label=LED B
PB13.Signal=GPIO_Output
PB14.GPIO_Label=LED C
PB14.Signal=GPIO_Output
PB15.GPIO_Label=LED D
PB15.Signal=GPIO_Output
PB6.Signal=USART1_TX
PB7.Signal=USART1_RX
PB8.Signal=I2C1_SCL
PB9.Signal=I2C1_SDA
PC0.GPIO_Label=INT_ACC
PC0.Signal=GPXTI0
PC1.GPIO_Label=INT_GYR
PC1.Signal=GPXTI1
PC10.Signal=USART3_TX
PC11.Signal=USART3_RX
PC2.GPIO_Label=MAGNET_INT
PC2.Signal=GPXTI2
PC3.GPIO_Label=BARO_INT
PC3.Signal=GPXTI3
PC9.Signal=I2C3_SDA
PH0-OSC_IN.Signal=RCC_OSC_IN
PH1-OSC_OUT.Signal=RCC_OSC_OUT
